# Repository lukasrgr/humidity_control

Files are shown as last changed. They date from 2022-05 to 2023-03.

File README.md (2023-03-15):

<p align="center">
<a href="https://github.com/Johle00" target="_blank">
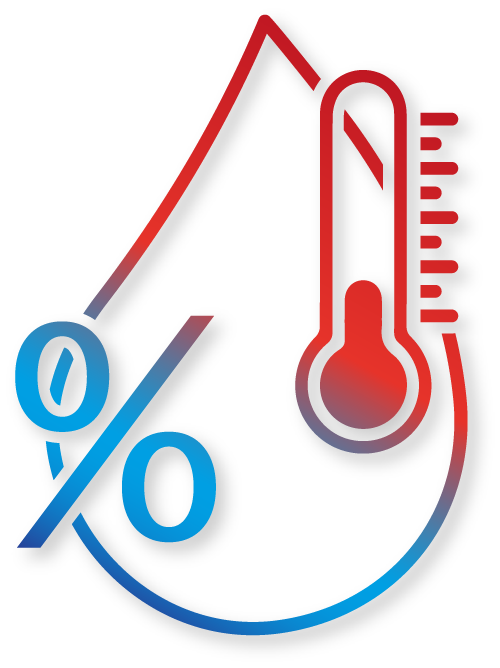
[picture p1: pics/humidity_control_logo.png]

</a>

<h1 align="center" top="0%">
Humidity_Control
</h1>
</p>

## Basics
This project aims at regulating our bathrooms humidity by controlling a dehumidifier. 
The humidity, temperature, current timestamp and the dehumidifier status is written into a database.
Using an UI, the user can observe how these values change over time.

<p align="center">
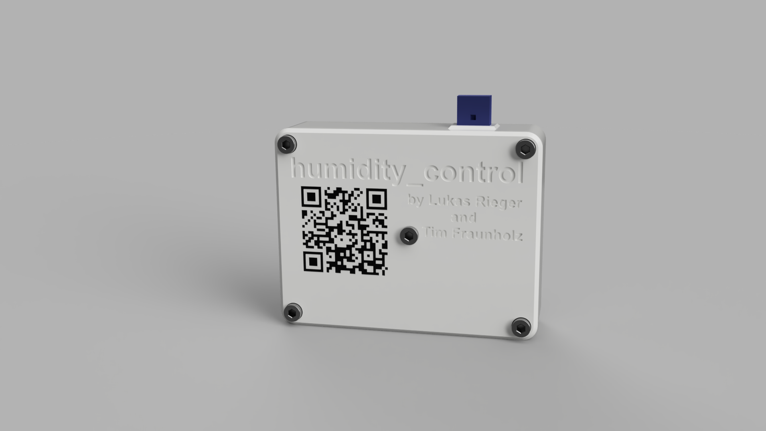
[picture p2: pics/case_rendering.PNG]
  
</p>

<!-- START doctoc generated TOC please keep comment here to allow auto update -->
<!-- DON'T EDIT THIS SECTION, INSTEAD RE-RUN doctoc TO UPDATE -->

**Table of Contents**
  - [Features](#features)
    - [Implemented features](#implemented-features)
    - [Possible future work](#possible-future-work)
    - [Intentional limitations](#intentional-limitations)
  - [Usage](#usage)
  - [Project structure](#project-structure)
  - [Implementation](#implementation)
    - [Hardware](#hardware)
    - [Mounting](#mounting)
    - [Establishing Communication](#sequencediagramm)
    - [Programming language and environment](#programming-language-and-environment)

<!-- END doctoc generated TOC please keep comment here to allow auto update -->

## Features
### Implemented features
* Measuring the humidity and temperature
* Controlling the dehumidifyer
* Transmitting data to the server, writing into the database
* Saving data up to one day on the ESP, if the database is temporarily unavailable
* Plotting the time series
* 3D printable housing
### Possible future work
* bidirectional Communication from UI -> Ui-handler -> Backend -> esp
* Backend: 
  * Queue in Backend to what periods have already been sent to UI
  * User authentification
  * Redo in Java
* UI: 
  * Add Global Translationservice
  * Changing the dehumidifier activation threshold using the UI
* Database:
  * dump
  * Setup script
### Intentional limitations
* No secure communication

## Usage
In the ESP code, you have to setup the WiFi connection and the target TCP socket for the database. Follow the instructions provided [here](hardware/esp_code/src/README.md).

Make sure the database and server are setup correctly. Adjust the server IP and port in 'configuration.h'.

## Project structure
Here are some directories that may contain interesting files. All of these contain a separate, more detailed readme:
* [/backend/](backend/README.md):
    - [Backend server](backend/backendServer.py), that handles incoming data from the ESP. Writes into a database.
    - [Middleend server](backend/middleEndServer.py) that handles incoming requests from Frontend, executes a query in the database, formats the result and sends this back to frontend.
* [/ui/](ui/README.md): The user interface.
* [/hardware/](hardware/README.md): Relevant Information for setup of microcontroller
    * [/wiring/](hardware/wiring/README.md): A basic wiring diagram
    * [/esp_code/](hardware/esp_code/): The ESP8266 code measuring values and controlling the dehumidifier.
    * [/3d_objects/](hardware/3d_objects/README.md): The printable case as STLs.
* [/pics/](pics/): Pictures

## Implementation
### Hardware
We used a ESP8266 NodeMCU board as our microcontroller. An AZ-Delivery relay board is used to turn the dehumidifier on and off. We switch both the neutral and the phase wire. We use a DHT11 humidity and temperature sensor due to its low price and its easy availability. If you want a more accurate reading, you could switch to a DHT22, but this would require a 3D model redesign.  

### Mounting
Please refer to the picture below for installing the components and wiring. You need a few short M3 screws and some cables.  
Mount the ESP using M3 screws. The ESP will be powered or programmed using its USB port.  
To hold the relay board in place, you have to install the board and then melt the mounting pins of the case. Connect the power and GND wires to the ESP. Connect the two signal wires to D2 and D3 of the ESP. One relay is for the phase, the other for neutral. Fix the cables using the wire_lid. Please be careful work when working with mains voltage.

<p align="center">
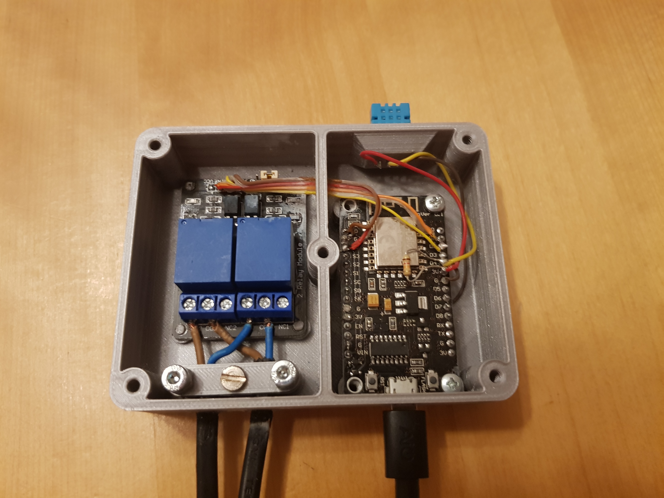
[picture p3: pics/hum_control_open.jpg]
  
</p>

### Sequencediagramm
##### This Chart visualizes the Communication between all components
\
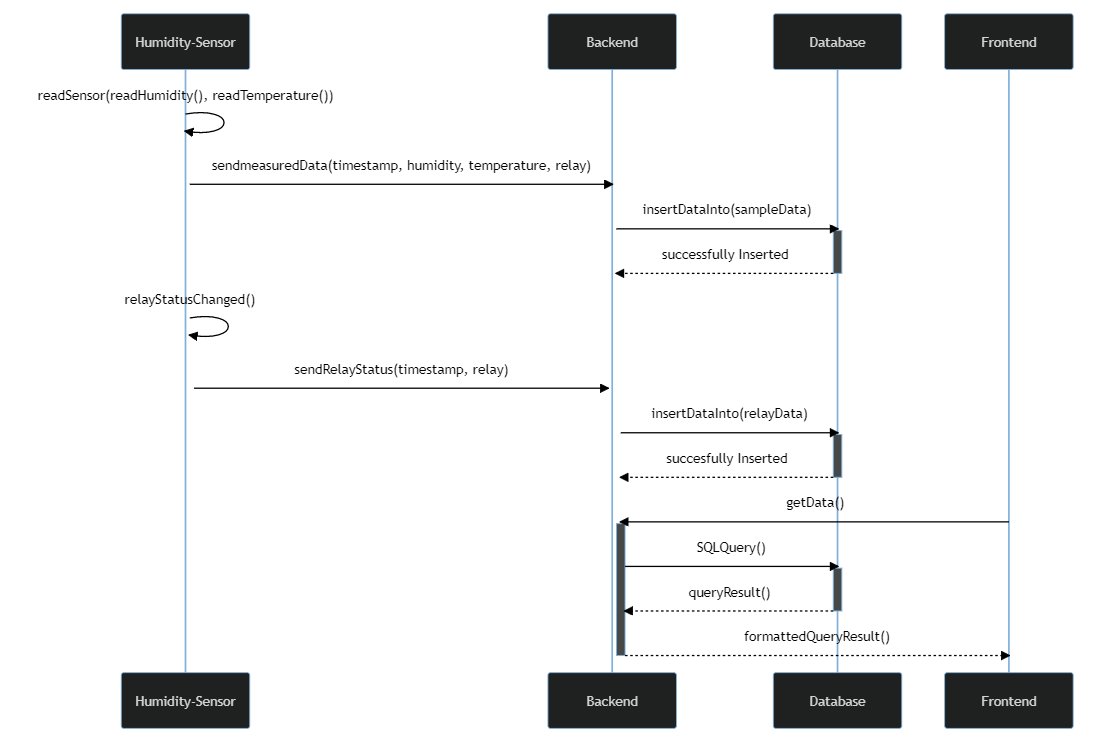
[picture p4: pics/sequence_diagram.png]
Installed hardware.
 

### Programming language and environment

Backend, Frontend and Database is running on
**Raspberry Pi 4 Model B 8 GB RAM**

| Component | Programming Language | Framework | In Detail 
| --- | --- | --- | --- |
| Database | MySQL | |MariaDB
| Backend | Python
| Frontend | Typescript & HTML | Angular & Ionic
| Hardware | C, C++ | Arduino |Esp8266

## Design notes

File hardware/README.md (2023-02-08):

# hardware

## Contents
* /3d_objects/: STL files for 3D printing.
* /esp_code/: The ESP8266 code measuring values and controlling the dehumidifier.
* /wiring/: A basic wiring diagram.

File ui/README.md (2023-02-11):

### Framework Details
# Ui

This project was generated with [Angular CLI](https://github.com/angular/angular-cli) version 13.3.4.\
`@Ionic` and `@Angular-Material` are also a part of this project.

## Development server

Run `npm install` to install all relevant packages.

If your node-version does not fit, look inside [package-lock.json](package-lock.json). Look for the `engines` param. Thats the best approach by now. Or on `ng serve` there will be a suggestion.

Run `ng serve` for a dev server. Navigate to `http://localhost:4200/`. The application will automatically reload if you change any of the source files.

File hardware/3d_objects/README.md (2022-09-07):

# 3D objects
Here you can find stl files to print. Printing most components with PLA is fine. The gasket needs to be printed with TPU. You need to add a color change if you want the QR code of the lid to work. You should seal all openings especially of the relay compartment, cyanoacrylate  super glue worked well for us.

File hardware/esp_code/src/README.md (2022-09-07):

# humidity_control

## Basics
The ESP8266 measures the humidity, controls the dehumidifier and sends data to a TCP socket.

## Features
### Implemented features
* Measuring the humidity and temperature
* Controlling the dehumidifyer
* Transmitting data to the server, writing into the database
* Saving data up to one day on the ESP, if the database is temporarily unavailable
### Possible future work
* Changing the dehumidifier activation threshold using the UI
### Intentional limitations
* No secure communication

## Usage
Enter your networks SSID and password in 'configuration.h'. You also have to enter you TCP sockets IP and port.

## Project structure
Here are some important files. To keep it brief, only the headers are listed:
* /dht_lib/: Here cou have to clone the library for the DHT11 sensor.
* /configuration.h: Configure WIFI settings and .
* /data_queue.h/: A ring buffer to store measured data. 
* /main.cpp/: Initializes hardware and triggers sensor reading and sending.
* /relay_activation.h/: Activate two relays.
* /socket_commun.h/: Writing data to the server.
* /types_and_enums.h/: Contains project wide typedefs.

## Implementation
The mysql connector lib is used. Build using PlatformIO.

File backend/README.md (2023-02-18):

## Getting Started

1. Define [confidentials](confidentials.py)
2. Execute the [backendServer](backendServer.py)
3. The according UI Handler can be found here [middleEndServer](middleEndServer.py).

## Sequencediagramm
\
Installed hardware.

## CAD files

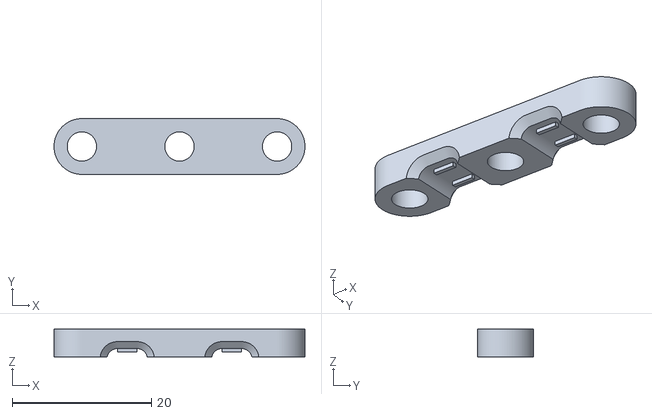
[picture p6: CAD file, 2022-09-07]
hardware/3d_objects/wire_lid_v1.stl
36.0 x 8.00 x 4.00

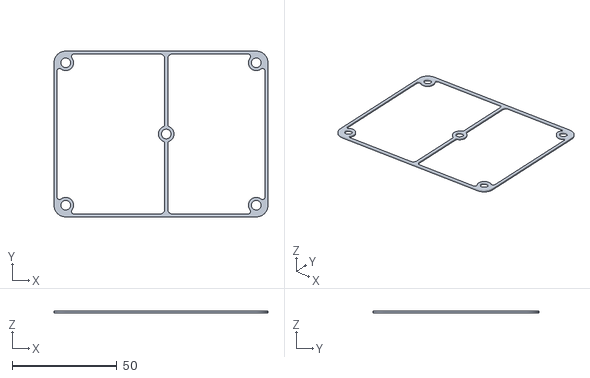
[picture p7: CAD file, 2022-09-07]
hardware/3d_objects/gasket_v1.stl
102.2 x 79.2 x 1.00

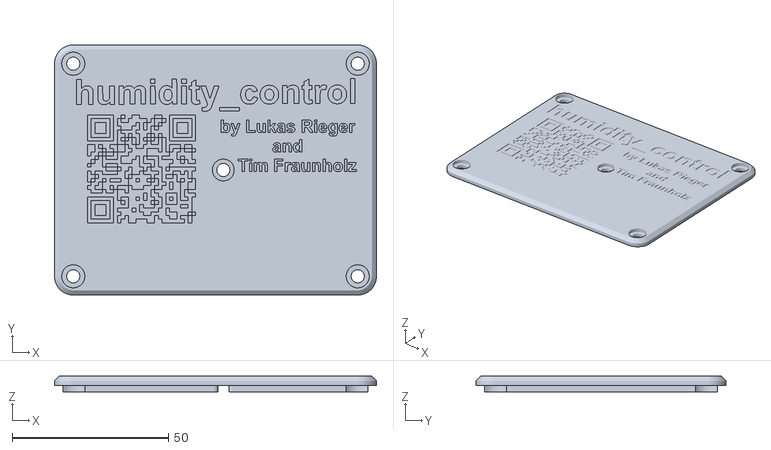
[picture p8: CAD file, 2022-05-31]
hardware/3d_objects/lid_writing_qr_v1.stl
103.0 x 80.0 x 5.00

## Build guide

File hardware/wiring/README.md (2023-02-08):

# Wiring 
This project uses only so few components, that I will not add a wiring diagram.  
Connect the two pins of your relay module to the pins specified in "relay_activation.cpp".  
Connect the DHT's data pin to the one specified in "main.cpp".

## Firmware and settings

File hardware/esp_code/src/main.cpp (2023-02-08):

/********************************** Includes **********************************/
#include <Arduino.h>
#include <stdbool.h>
#include <DHT_U.h>
#include "ESP8266WiFi.h"
#include "time.h" // setenv(), do not worry about IDE warning, compiles fine
#include "configuration.h"
#include "relay_activation.h"
#include "types_and_enums.h"
#include "data_queue.h"
#include "socket_communication.h"


/********************************** Defines ***********************************/
#define DHT_PIN D4
#define DHT_TYPE DHT11
#define RELAY_NUM 2


/********************************* Constants **********************************/ 
// Configure your ssid and password here
const char ssid[] = YOUR_SSID;
const char pass[] = YOUR_PASSWORD;


/***************************** Struct definitions *****************************/
/**************************** Prototype functions *****************************/
bool check_and_activate_relay(float hum, float temp, uint32_t timestamp);
dht_data_t measure_until_data();
void wait_until_round_time();
void error_handler();


/**************************** Variable definitions ****************************/
DHT dht(DHT_PIN, DHT_TYPE);

uint32_t last_executed = 0;


/**************************** Function definitions ***************************/
void setup() {
  // put your setup code here, to run once:
  Serial.begin(9600);
  delay(50);

  printf("\n\rHello\n\r");

  setup_relays();

  /* 
   * Check for possible errors.
   */
  if (ON_HUM_THRES < OFF_HUM_THRES)
  {
    printf("Threshold range error detected, aborting\n\r");
    error_handler();
  }

  setup_data_queue();

  /*
   * This allows the correct timeoffset to be used for localtime().
   * Do not worry about the IDE warning, the function is defined in a macro.
   */
  setenv("TZ", "CET-1CEST,M3.5.0,M10.5.0/3", 3);

  dht.begin();

  printf("hum %f temp %f\n\r", dht.readHumidity(), dht.readTemperature());

  printf("Trying to connect to %s\n\r", ssid);
  WiFi.begin(ssid, pass);
  while (WiFi.status() != WL_CONNECTED) {
    delay(500);
    Serial.print(".");
  }
  Serial.print(WiFi.macAddress());
  printf("Connected.\n\r");
  Serial.println("My IP address is: ");
  Serial.println(WiFi.localIP());
  printf("\n\r");

  setup_user_comm();

  wait_until_round_time();
}

void loop() {
  const uint32_t DATA_TIME_OFFSET_UNIX = SAMPLE_EVERY_MIN * 60;

  static time_t next_data_time = 0;

  time_t rawtime;
  time(&rawtime);

  // Get new data
  dht_data_t new_dat = measure_until_data();
  new_dat.timestamp = (uint32_t)rawtime;

  // Activate relay if necessary
  new_dat.relay_active = check_and_activate_relay(new_dat.humidity, 
                                                  new_dat.temp,
                                                  new_dat.timestamp);
  
  if (rawtime >= next_data_time)
  {

#ifdef PRINTS_IN_MAIN
    printf("Aquired new hum %u, temp %u\n\r", new_dat.humidity, new_dat.temp);
    printf("elements_in_buf() %i \n\r", elements_in_buf());
#endif // PRINTS_IN_MAIN

    push_data_element(new_dat);

    // Round to next value
    next_data_time = DATA_TIME_OFFSET_UNIX * 
        ((rawtime + DATA_TIME_OFFSET_UNIX) / DATA_TIME_OFFSET_UNIX);
  }

  send_dht_data_from_queue();
}

/* 
 * Keep measuring until data is valid.
 * The dht lib returns 'nan' from time to time, so this function is needed.
 * 
 * @return: A dht_data_t element.
 */
dht_data_t measure_until_data()
{
  dht_data_t new_dat = {0};

  float humid = 0;
  float temp = 0;
  bool data_valid = false;
  while (!data_valid)
  {
    humid = dht.readHumidity();
    temp = dht.readTemperature();

    data_valid = !isnan(humid) && !isnan(temp);
  }

  new_dat.humidity = (uint8_t)humid;
  new_dat.temp = (uint8_t)temp;

  return new_dat;
}

/* 
 * Check if the humidity exceeds the desired threshold.
 * If so activate the relay and thus the dehumidifyer.
 * 
 * @param hum:  The current humidity.
 * @param temp: The current temperature.
 * @return: Relay status.
 */
bool check_and_activate_relay(float hum, __attribute__((unused)) float temp,
                              uint32_t timestamp)
{
  static bool relay_active = false;

  if (hum >= ON_HUM_THRES)
  {
    if (!relay_active)
    {
      activate_first_n_relays(RELAY_NUM);
      send_relay_set(timestamp);
      relay_active = true;
    }
  } 
  else if (hum <= OFF_HUM_THRES)
  {
    if (relay_active)
    {
      deactivate_n_relays(RELAY_NUM);
      send_relay_reset(timestamp);
      relay_active = false;
    }
  }
  return get_relay_status(1);
}

/* 
 * Wait until a multiple of 5 minutes is reached.
 * 
 * @return: None.
 */
void wait_until_round_time()
{
  time_t rawtime;
  time(&rawtime);

  while(rawtime % ((SAMPLE_EVERY_MIN)*60) != 0)
  {
    time(&rawtime);
    yield();
  }
}

/* 
 * Infinite loop if an error occurs.
 * 
 * @return: None.
 */
void error_handler()
{
  printf("Error detected, halting.\n\r");
  deactivate_n_relays(RELAY_NUM);
  for(;;)
    yield();
}

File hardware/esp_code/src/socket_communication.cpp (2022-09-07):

/********************************** Includes **********************************/
#include "socket_communication.h"
#include <string.h>
#include <stdbool.h>
#include "ESP8266WiFi.h"
#include "data_queue.h"


/********************************** Defines **********************************/
#define USER_SCKT_BUF_LEN 256
#define JSON_MAX_LEN 256


/********************************* Constants **********************************/
/***************************** Struct definitions *****************************/
/**************************** Prototype functions *****************************/
int send_one_generic_string(const char *buf, size_t buf_len);


/**************************** Variable definitions ****************************/
WiFiServer wifiServer(23);
WiFiClient tcp_client;
bool connected = false;

char user_socket_buf[USER_SCKT_BUF_LEN] = {};
bool user_data_available = false;

const uint16_t port = SERVER_PORT;
IPAddress ip_to_conn = IPAddress(SERVER_IP);

// TODO Do not fix the size
char json_template[JSON_MAX_LEN] = "{ \"method\":\"sendGeneralData\", "
                                    "\"timestamp\":%u, \"humidity\":%u, "
                                    "\"temperature\":%u , \"relay\":%u }";
char relay_json_template[JSON_MAX_LEN] = "{\"method\": \"sendRelayData\", "
                                    "\"timestamp\": %u, \"relay\": %u }";
char json_loc[JSON_MAX_LEN];

/**************************** Function definitions ****************************/
/*
 * Setup the user communication.
 * 
 * @return: Success status.
 */
int setup_user_comm()
{
    wifiServer.begin();
    return 0;
}

int dummy_client()
{
    snprintf(json_loc, JSON_MAX_LEN, json_template, 1234, 1, 2);
    if (!tcp_client.connect(ip_to_conn, port))
    {
        Serial.println("Connection to host failed");
        delay(1000);
        return 1;
    }
    Serial.println("Connected to server successful!");
    delay(250);
    tcp_client.print(json_loc);
    Serial.print('\n');
    tcp_client.stop();
    delay(5000);
    return 0;
}

/* 
 * Send a generic string to the database.
 * TODO These delays seem to be unneccessary or massively overdimensioned. 
 * 
 * @param buf: The string buffer to send.
 * @param buf_len: The length of the string buffer.
 * @return: Success status.
 */
int send_one_generic_string(const char *buf, size_t buf_len)
{
    if (!tcp_client.connect(ip_to_conn, port))
    {
        Serial.println("Connection to host failed");
        delay(1000);
        return 1;
    }
    Serial.println("Connected to server successfully!");
    delay(250);
    tcp_client.print(buf);
    Serial.print('\n');
    tcp_client.stop();
    delay(5000);
    return 0;
}

/* 
 * Try to send one dht_data_t.
 * 
 * @return: Success status, 0 if sent.
 */
int send_one_dht_data(dht_data_t *dat)
{
    snprintf(json_loc, JSON_MAX_LEN, json_template, dat->timestamp, 
                dat->humidity, dat->temp, dat->relay_active);
    return send_one_generic_string(json_loc, strlen(json_loc));
    /*
    if (!tcp_client.connect(ip_to_conn, port))
    {
        Serial.println("Connection to host failed");
        delay(1000);
        return 1;
    }
    Serial.println("Connected to server successfully!");
    delay(250);
    tcp_client.print(json_loc);
    Serial.print('\n');
    tcp_client.stop();
    delay(5000);
    return 0;
    */
}

/* 
 * Send a relay set message to the database.
 * 
 * @param timestamp: The current time.
 * @retval: Success status.
 */
int send_relay_set(uint32_t timestamp)
{
    snprintf(json_loc, JSON_MAX_LEN, relay_json_template, timestamp, 1);
    return send_one_generic_string(json_loc, strlen(json_loc));
}

/* 
 * Send a relay reset message to the database.
 * 
 * @param timestamp: The current time.
 * @retval: Success status.
 */
int send_relay_reset(uint32_t timestamp)
{
    snprintf(json_loc, JSON_MAX_LEN, relay_json_template, timestamp, 0);
    return send_one_generic_string(json_loc, strlen(json_loc));
}

/* 
 * Send data from the data_queue if available.
 * Needs to be called in a loop.
 * 
 * @return: Success status.
 */
int send_dht_data_from_queue()
{
    static dht_data_t data_to_send = {0};

    int status = 1;

    // No data if timestamp = 0.
    if (data_to_send.timestamp == 0)
    {
        if (elements_in_buf() > 0)
        {
            data_to_send = pop_data_element();
#ifdef SEND_DEBUG
            printf("Fetched new data to send: ");
            printf("[%u, %i, %i, %i]\n\r", data_to_send.timestamp, data_to_send.humidity, 
				data_to_send.temp, data_to_send.relay_active);
#endif // SEND_DEBUG
        }
    }
    else
    {
        status = send_one_dht_data(&data_to_send);
        // Reset static variable if data has been successfully been sent.
        if (status == 0)
        {
            memset(&data_to_send, 0, sizeof(data_to_send));
#ifdef SEND_DEBUG
            printf("Successfully transmitted data.\n\r");
#endif // SEND_DEBUG
        }
    }

    return status;
}

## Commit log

2022-03-24 added initial files and adafruit DHT lib
    [configuration.h]
2022-03-24 tried mysql connector code, not yet working
    [configuration.h]
2022-04-06 > Inserting into DB humidity > table sampleData works
2022-04-24 dummy socket comm and data queue
    [configuration.h]
2022-04-27 restructured repo
    [configuration.h]
2022-05-02 add new column relay to table
2022-05-20 > show first sampleData in UI > update uihandler and echo-server > add tile for consumptionPriceCalculation for electricity of dehumidifier > add tile for generalDataOverview: Relay, Temperature, Hum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
2022-05-24 changed activation values, changed relay, added initial print files
    [Body1.stl, configuration.h, dht_casing.stl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]
2022-05-31 started readmes, improved esp configuration
    [Body1.stl, configuration.h, dht_casing.stl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]
2022-09-07 added communication for relay status, readme
    [configuration.h]
2022-09-07 updated 3D files, rendering and readme
    [Body1.stl, configuration.h, dht_casing.stl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]
2022-12-28 > introduce tiles in dashboard for humidty, temperature, and relayState
2023-01-05 Fixed a bug where the wrong relay value was read.
    [main.cpp]
2023-02-03 added Datepicker to chart added angular material library created tile for lastDatapoint in database
2023-02-08 changed wiring readme, there will be no wiring diagram
2023-02-18 reverting squashing
    [configuration.h, gasket_v1.stl, lid_writing_qr_v1.stl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]
